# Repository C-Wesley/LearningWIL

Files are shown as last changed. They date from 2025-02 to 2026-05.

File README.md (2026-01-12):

# LearningWIL

**Water Is Life (WIL)** is an Autonomous Surface Vehicle (ASV) developed for Augusta Utilities as part of an internship collaboration with Augusta University.

This repository serves as a learning and continuation guide for future developers. It documents the programming, electronics, and system architecture required to understand and extend WIL.

## Project Overview

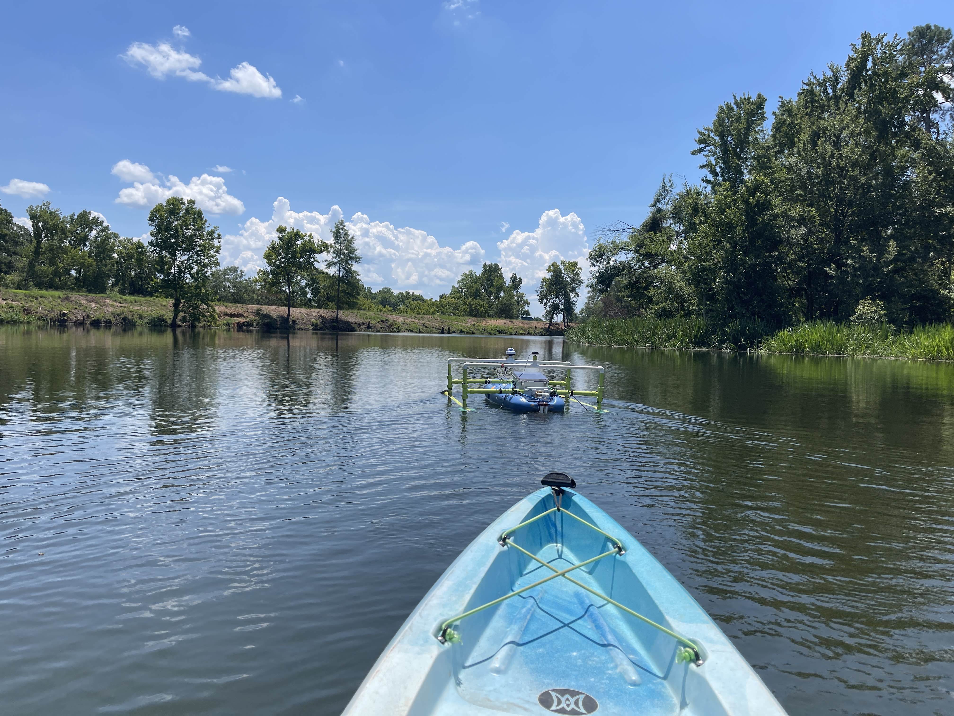
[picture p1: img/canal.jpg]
WIL in the Canal

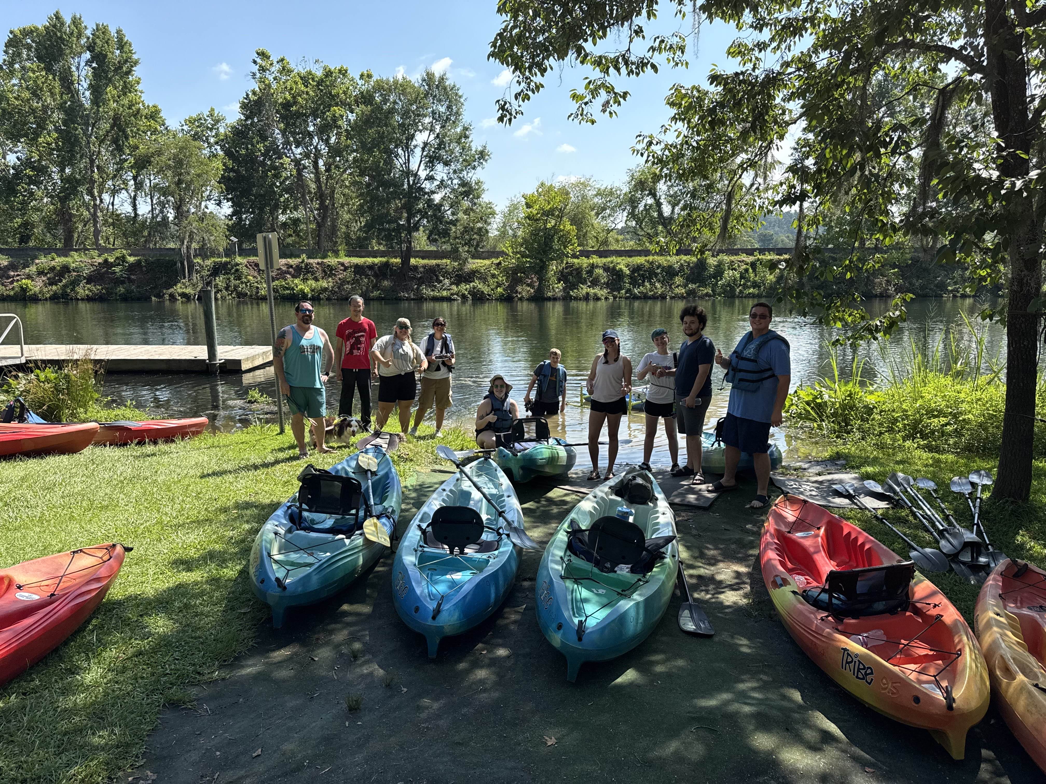
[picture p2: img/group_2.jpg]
WIL canal group RAGU Group Photo

WIL at Lake Olmstead

WIL is designed for environmental data collection and autonomous navigation of local waterways. Development spans embedded programming, sensor integration, data logging, and vehicle controls.

## Repository Structure

### 1. Beginner Examples
`Beginner Examples/`

This is the recommended starting point for new contributors.

- Build circuits 
- Type the code (do not copy–paste)
- Learn how each sensor works in isolation

Suggested exercises:
- Move the IMU and visualize data using the **Arduino Serial Plotter**
- Observe GPS latitude/longitude changes while stationary vs. moving
- Combine GPS, heading, and SD card logging into a simple data logger!

These examples are for you to better understand each sensor individually before trying to throw all of them together. 
They are the 'building blocks' so to speak of WIL. 

### 2. Class-Based Examples
`Class Based Examples/`

These examples introduce **Object-Oriented Programming (OOP)** in C++.

Example:
```cpp
File myFile = ...
```
This creates a `File` object, which:

- Encapsulates data related to files
- Provides methods (functions) that operate on that data

Using classes helps:

- Organize complex systems
- Isolate bugs
- Scale the codebase as features grow

### 3. Notebooks
`Notebooks/`

This directory contains a digital copy of the lab notebooks for WIL. Not every entry is directly related to WIL. Some were more for my own learning. However, there are several useful entries to help you get more familiar with WIL. In the Beginner Examples, I've linked the related entires on each sensors readme file.

### 4. WIL Development Code

`WILDev/`

This directory contains the arudino code running on:

- WIL (Arduino Giga)
- The remote controller (MKR 1310)

Subdirectories:

- `new code/` – current class-based implementation
- `old code/` – old version (no classes)

New development should be based on `new code/`.

## System Architecture

WIL is generally structured around the following diagrams.

 **:TODO:** Update class diagram to reflect latest architecture.

### Class Diagram

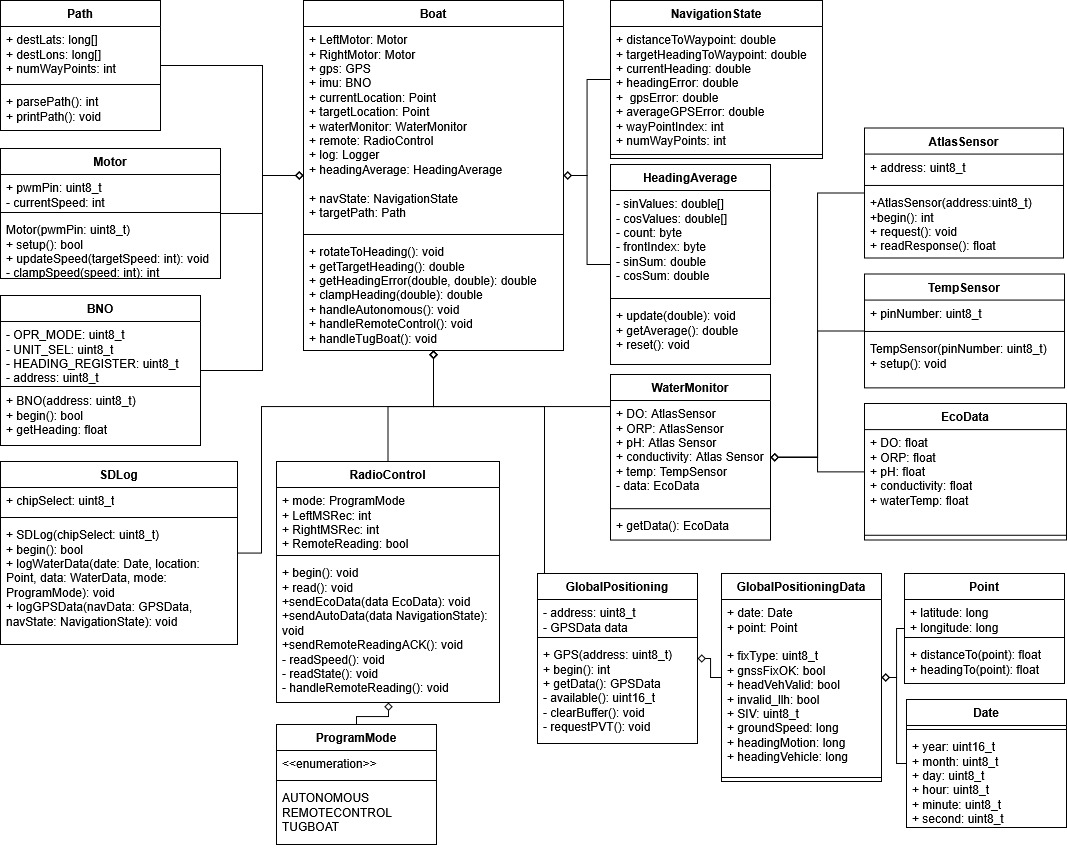
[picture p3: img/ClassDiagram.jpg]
WIL Class Diagram


### Block Diagram

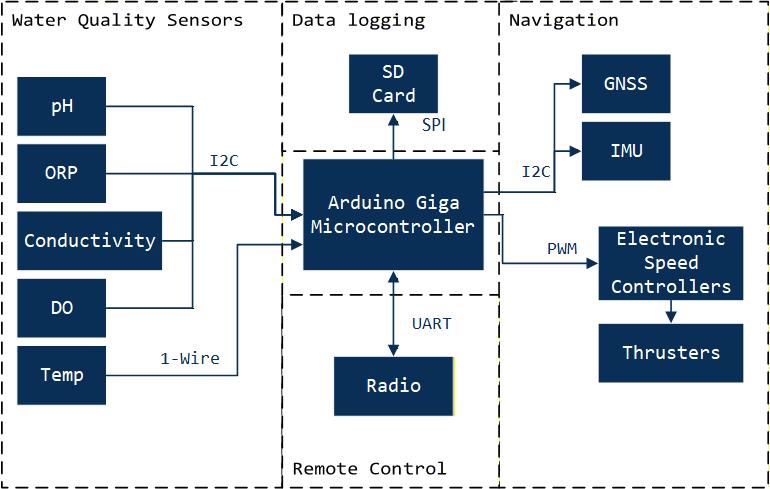
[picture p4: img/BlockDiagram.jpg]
WIL Block Diagram


## Contributing

This repository is designed to be learned from, modified, and extended. Developers are encouraged to:

- Experiment
- Break things
- Document findings
- Improve clarity for the next developer

Water is life (and so is maintainable code).

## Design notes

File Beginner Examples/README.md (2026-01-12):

# Beginner Examples

This folder contains stand-alone Arduino sketches intended to introduce different functionalities of WIL through examples. Each program focuses on one idea at a time to help you learn all the different components of WIL. Here, I am not using classes or object oriented programming because it is easier to learn that way. 
  
These examples are meant to give you understanding of how each subsystem of WIL works as well as build your skills with communication protocols on arduino like I2C, UART, and SPI. 

I recommend building the circuits, typing the code from scratch, and experimenting with each sensor that you use. Typing the code from scratch will help you understand better and aid when reading the entire code base of WIL later on. 

# Recommended Learning Order
- basic_imu
- basic_gps
- basic_sd_card
- basic_thrusters
- basic_sensors
- basic_radio

Most examples have several levels of understanding. Take the GPS for instance. It has both a library version and a non library version. If your goal is to just use the data from the sensor, use the library to make it easy. If your goal is to better understand I2C, take a look at the 'no-library-challenge'. It's not for the faint of heart!

As WIL grew into a more complex system, writing code in the style of these examples became difficult to maintain and extend. To address this, the project transitioned to using classes, which allowed functionality to be separated into well-defined components and enabled data and system state to be encapsulated more cleanly. However, starting here is crucial to your understanding of how the components work and provides a place to experiment, make mistakes, and learn before moving on to more complex programs.

In general, the development approach used throughout this project is to isolate and understand one piece of the system at a time before integrating it into the larger whole. These examples are a direct result of learning how to use individual sensors, peripherals, and interfaces in isolation prior to combining them into a complete system.

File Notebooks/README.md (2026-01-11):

# Lab Notebook entries

## Notebook 1 Contents 
0. [Table of Contents](Notebook_1/0_Table_Of_Contents.pdf)
1. [Arduino MKR 1310 Board](Notebook_1/1_2_Arduino_MKR_1310_Board.pdf)
2. [BNO055 Testing](Notebook_1/3_BNO055_Testing.pdf)
3. [DFRobot GNSS](Notebook_1/4_DFRobot_GNSS.pdf)
4. [Standalone GNSS Data Logger](Notebook_1/5_Standalone_GNSS_Data_Logger.pdf)
5. [Level Shifting MOSFET](Notebook_1/6_Level_Shifting_MOSFET.pdf)
6. [Programming the ALS31313 I2C Address](Notebook_1/7_Programming_the_ALS31313_I2C_address.pdf)
7. [Reyax RYS8839 NEMA Parsing and Logging](Notebook_1/8_Reyax_RYS8839_NEMA_Parsing_and_Logging.pdf)
8. [SparkFun ZED-F9P Logging](Notebook_1/9_Sparkfun_ZED-F9P_Logging.pdf)
9. [Setting Up an RTK Base and Rover System](Notebook_1/10_Setting_up_an_RTK_Base_and_Rover_System.pdf)
10. [BNO055 Relative Heading Observation](Notebook_1/11_BNO055_Relative_Heading_Observation.pdf)
11. [Blue Robotics T200 Underwater Thruster](Notebook_1/12_Blue_Robotics_T200_Underwater_Thruster.pdf)
12. [Autonomous WIL](Notebook_1/13_Autonomous_WIL.pdf)
13. [Writing an H-Bridge Library](Notebook_1/14_Writing_an_H-Bridge_Library.pdf)
14. [Writing an ESC Library](Notebook_1/15_Writing_an_ESC_Library.pdf)
15. [Writing a GPS Library](Notebook_1/16_Writing_a_GPS_Library.pdf)
16. [Writing a BNO Library](Notebook_1/17_Writing_a_BNO_Library.pdf)
17. [Writing a Controller Library](Notebook_1/18_Writing_a_Controller_Library.pdf)
18. [Fixing the Arc](Notebook_1/19_Fixing_the_Arc.pdf)
19. [Writing a Heading Control Library](Notebook_1/20_Writing_a_Heading_control_Library.pdf)
20. [Putting It All Together: Land & Water](Notebook_1/21_22_Putting_it_all_Together_Land_Water.pdf)

## Notebook 2 Contents
0. [Table of Contents](0_Table_of_Contents.pdf)
1. [Land Testing](1_Land_Testing.pdf)
2. [Walking at Lake Olmstead](2_Walking_at_Lake_Olmstead.pdf)
3. [The Better Figure 8](3_The_Better_Figure_8.pdf)
4. [Canal Testing](4_Canal_Testing.pdf)
5. [MB1005 Parksonar Sensor](5_MB1005_Parksonar_Sensor.pdf)
6. [Lidar for Object Detection](6_Lidar_for_Object_Detection.pdf)
7. [Land Testing with Lidar](7_Land_Testing_with_Lidar.pdf)
8. [Revisiting the BNO055](8_Revisiting_the_BNO055.pdf)
9. [Fixing the Negative Heading](9_Fixing_the_Negative_Heading.pdf)
10. [Revisiting the SparkFun GPS](10_Revisiting_the_Sparkfun_GPS.pdf)
11. [Logging and Plotting GPS Data on My Maps](11_Logging_and_Plotting_GPS_Data_on_My_Maps.pdf)
12. [Adding Timestamps from the SparkFun GPS](12_Adding_Timestamps_from_the_Sparkfun_GPS.pdf)
13. [Integrating the New BNO and GPS Code](13_Integrating_the_New_BNO_and_GPS_Code.pdf)
14. [SparkFun GNSS with the Library](14_Sparkfun_GNSS_with_the_library.pdf)
15. [Design Notes](15_Design_Notes.pdf)
16. [Battery Maintenance](16_Battery_Maintenance.pdf)
17. [Basics of SD Card](17_Basics_of_SD_Card.pdf)
18. [Surface Mount Soldering Notes](18_Surface_Mount_Soldering_Notes.pdf)
19. [DOpTC Integration with Arduino Giga](19_DOpTC_Integration_with_Arduino_Giga.pdf)
20. [1-Wire Digital Thermometer DS18B20](20_1-Wire_Digital_Thermometer_DS1B20.pdf)
21. [Introduction to Particle Functions and Variables](21_Introduction_to_Particle_Functions_and_Variables.pdf)
22. [Reading DOpTC Faster](22a_Reading_DOpTC_Faster.pdf)
23. [DOpTC I2C Bus Integration](22_DOpTC_I2C_Bus_Integration.pdf)
24. [Reading the Number of Available Bytes (ZED-F9P)](23_Reading_the_Number_of_Available_Bytes_ZED-F9P.pdf)
25. [Notes on the UBX Protocol for the ZED-F9P](24_Notes_on_the_UBX_Protocol_for_the_ZED-F9P.pdf)
26.  [Reading NAV-PVT on the ZED-F9P without a library](24a_reading_NAVPVT_without_library.pdf)
27. [KiCad Workflow](25_KICAD_Workflow.pdf)
28. [Processing the NAV-PVT Message on ZED-F9P](26_Processing_the_NAV-PVT_Message_on_ZED-F9P.pdf)
29. [Using u-center to Configure the ZED-F9P](27_Uising_U-Center_to_Configure_the_ZED-F9P.pdf)
30. [Loft, Shell, and Boolean Tools in Onshape for Remote Control](28_Loft_Shell_Boolean_tools_Onshape_for_Remote_Control.pdf)
31. [Fitting Data with GNUPlot and Matplotlib](29_Fitting_Data_GNUPlot_and_Matplotlib.pdf)
32. [Eco Test at Lake Olmstead](30_Eco_Test_at_Lake_Olmstead.pdf)
33. [Notes on Floats](31_Notes_on_Floats.pdf)
34. [Serial Radio Basics](32_Serial_Radio_Basics.pdf)
35. [Serial Radio Advanced](32a_Serial_Radio_Advanced.pdf) 
36. [CNC Basics: V-Carve](33_CNC_Basics_V-Carve.pdf)

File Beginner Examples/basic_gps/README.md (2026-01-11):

# Global Navigation Satellite System 
We are using the sparkfun ZED F9P GNSS reciever.  

<a href="https://www.sparkfun.com/sparkfun-gps-rtk-sma-kit.html" target="_blank">Sparkfun GNSS SMA Kit</a>

Objectives:
-Use the Sparkfun GNSS Library to get location information

We used a MKR1310 microcontroller. Any 3.3v logic microcontroller should work. 

<a href="https://docs.arduino.cc/hardware/mkr-wan-1310/" target="_blank">MKR1310</a>

Connections for using I2C:

| MKR1310 |Sparkfun GNSS | 
|--- |---|
| 3.3v | 3.3v | 
| GND | GND |
| SDA | SDA |
| SCL | SCL |

To install the boards manager for the 1310, go to tools -> board -> board manager. 
Search "SAMD" and look for the arduino SAMD boards.

To install the library go to tools -> manage libraries
Search "SparkFun GNSS v3".

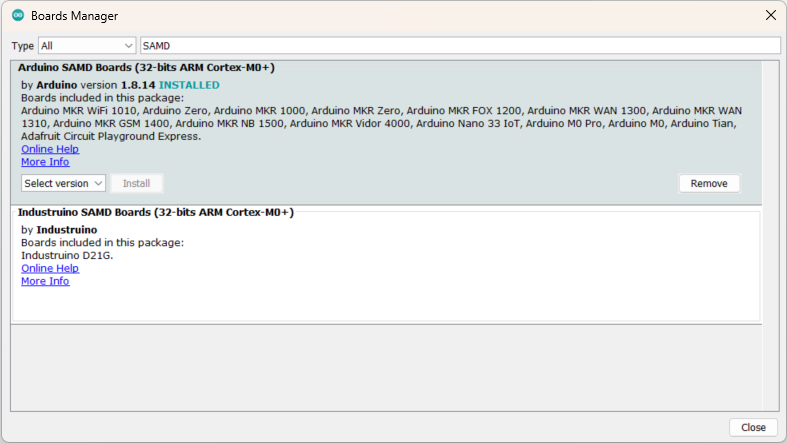
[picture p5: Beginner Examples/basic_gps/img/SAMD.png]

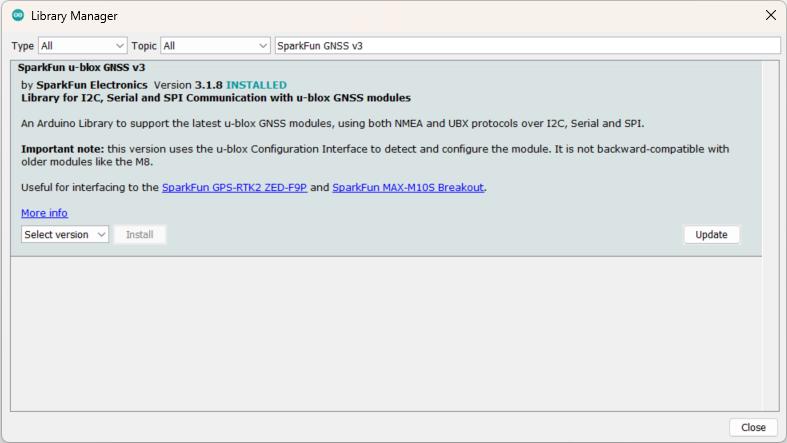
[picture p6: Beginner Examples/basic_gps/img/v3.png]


## u-blox ZED-F9P GNSS (I²C)

**What the Program Does**
- Initializes a ZED-F9P GNSS module
- Reads:
  - Latitude and longitude
  - Time and date
  - Satellites in view (SIV)
- Prints raw GNSS data to Serial

# Related Lab Notebook Entries

## No-Library-Challenege 
[Revisiting the ZED-F9P](https://c-wesley.github.io/projects/asv/Notebook_2/10_Revisiting_the_Sparkfun_GPS.pdf)

[Reading the Number of Available Bytes ZED-F9P](https://c-wesley.github.io/projects/asv/Notebook_2/23_Reading_the_Number_of_Available_Bytes_ZED-F9P.pdf)

[Notes on the UBX Protocol for the ZED-F9P](https://c-wesley.github.io/projects/asv/Notebook_2/24_Notes_on_the_UBX_Protocol_for_the_ZED-F9P.pdf)

[Reading the NAV-PVT on the ZED-F9P without a Library](https://c-wesley.github.io/projects/asv/Notebook_2/24a_reading_NAVPVT_without_library.pdf)

[Processing the NAV-PVT Message on the ZED-F9P](https://c-wesley.github.io/projects/asv/Notebook_2/26_Processing_the_NAV-PVT_Message_on_ZED-F9P.pdf)

[Using U-Center to Configure the ZED-F9P](https://c-wesley.github.io/projects/asv/Notebook_2/27_Uising_U-Center_to_Configure_the_ZED-F9P.pdf)

## SparkFun GNSS V3 Library 

[SparkFun ZED-F9P Data Logger](https://c-wesley.github.io/projects/asv/Notebook_1/9_Sparkfun_ZED-F9P_Logging.pdf)

[SparkFun GNSS with the Library](https://c-wesley.github.io/projects/asv/Notebook_2/14_Sparkfun_GNSS_with_the_library.pdf)

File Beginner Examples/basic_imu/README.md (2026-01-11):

# BNO055 IMU

This sketch does the following: 

- Scans the I²C bus to confirm the BNO055 address (0x28)
- Configures the BNO055:
- - uses the accelerometer and gyroscope in a fusion mode
- - Sets output units to degrees
- Reads the heading registers (0x1A and 0x1B)
- Combines the raw bytes and converts them to degrees

# Related Lab Notebook Entries

## No-Library-Challenge
[Revisiting the BNO055](https://c-wesley.github.io/projects/asv/Notebook_2/8_Revisiting_the_BNO055.pdf)

## Adafruit_Sensor and Adafruit_BNO055 Library
[BNO055 Testing](https://c-wesley.github.io/projects/asv/Notebook_1/3_BNO055_Testing.pdf)

The following resource was used when making the above: 
[Paul McWhorter IMU Videos](https://toptechboy.com/arduino-based-9-axis-inertial-measurement-unit-imu-based-on-bno055-sensor/)

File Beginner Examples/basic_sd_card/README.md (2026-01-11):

# SD Card
These files show the basics of using the sd card. 
The main objectives here are to:
- Initalize SD Card
- Handle SD errors
- Write to a file
- Determine if a file already exists
- Delete a file if it exists
- Extract data from a file into appropriate data types

## SD Card Write & Read

### Example 1: Writing and Reading a File

**What the Program Does**
- Initializes an SD card
- Deletes an existing file if present
- Writes text and numeric data to `data.txt`
- Reopens the file and prints its contents to Serial
---

### Example 2: Reading and Parsing a CSV File

**What the Program Does**
- Opens a CSV file (`path.csv`)
- Reads one line at a time
- Parses ID, longitude, and latitude fields
- Prints parsed data to Serial

Begin by looking at SD_Card_RW. 
Then move onto path_parse.

An advanced user may find the SD class and File class API useful (Located near the bottom of the page): 

<a href="https://docs.arduino.cc/libraries/sd/#SD%20class" target="_blank">Arduino SD Class API</a>

<a href="https://docs.arduino.cc/libraries/sd/#File%20class" target="_blank">Arduino File Class API</a>

The following connections need to be made to an appropriate microcontroller: 
For the purpose of this demonstration, we are using a 3.3v microsd card reader, so we opted for the arduino mkr1310 board for it's 3.3v logic. Chip select may be any unused digital pin. 

|SD Card| MKR1310 |
|---|---|
|MOSI | MOSI |
|MISO | MISO |
|SCK | SCK |
|CS | 5 |
|PWR | VCC | 
|GND | GND | 

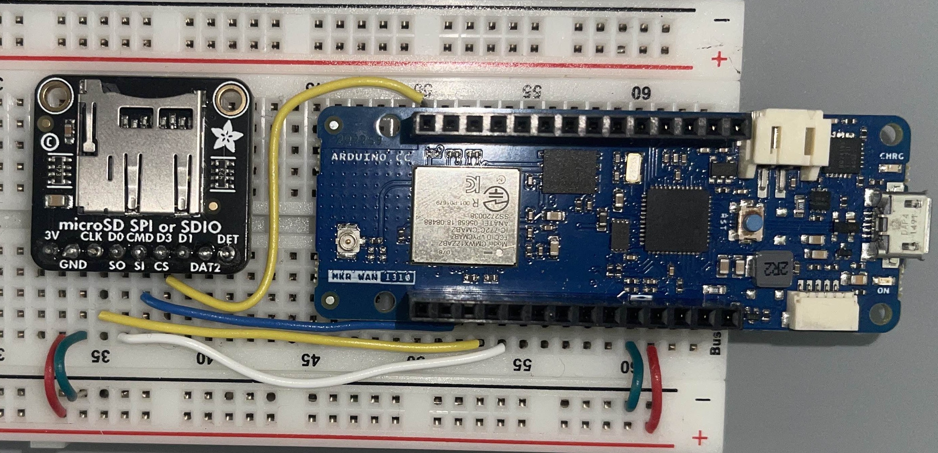
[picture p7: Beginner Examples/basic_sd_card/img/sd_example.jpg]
Example Connections

Figure 1. Example connections to the MKR 1310 board. 

# Related Lab Notebook Entries

[Basics of SD Card](https://c-wesley.github.io/projects/asv/Notebook_2/17_Basics_of_SD_Card.pdf)

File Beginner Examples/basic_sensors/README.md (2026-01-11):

# Related Lab Notebook Entires

[Reading DOpTC Faster](https://c-wesley.github.io/projects/asv/Notebook_2/22a_Reading_DOpTC_Faster.pdf)

[1-Wire Digitasl Thermometer DS18B20 (No Library)](https://c-wesley.github.io/projects/asv/Notebook_2/20_1-Wire_Digital_Thermometer_DS1B20.pdf)

## Older Implementation but still may be of use
[DOpTC Integration with Arduino Giga](https://c-wesley.github.io/projects/asv/Notebook_2/19_DOpTC_Integration_with_Arduino_Giga.pdf)

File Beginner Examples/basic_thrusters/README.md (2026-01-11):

# Thruster Controls
We are using two Blue Robotics T200 thrusters and their Basic Electronic Speed Controllers (ESC).

<a href="https://bluerobotics.com/store/thrusters/t100-t200-thrusters/t200-thruster-r2-rp/" target="_blank">T200 Thruster</a>

<a href="https://bluerobotics.com/store/thrusters/speed-controllers/besc30-r3//" target="_blank">Basic ESC</a>

<a href="https://bluerobotics.com/store/comm-control-power/powersupplies-batteries/battery-lp-4s-10ah/" target="_blank"> Lithum Polymer Battery </a>

Objectives:
-Understand PWM Control of T200's
-Use the Serial Monitor to test different speeds

The T200 thrusters use a three phase brushless motor.
You can think of each phase as a separate coil that is wraped around a stator. 
These coils are energized following a pattern to make the rotor spin. See diagram below. 

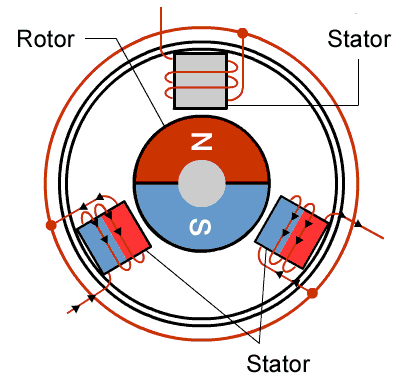
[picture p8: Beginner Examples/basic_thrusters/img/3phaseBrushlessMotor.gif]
Three Phase Motor Diagram


Example Wiring Diagram: 
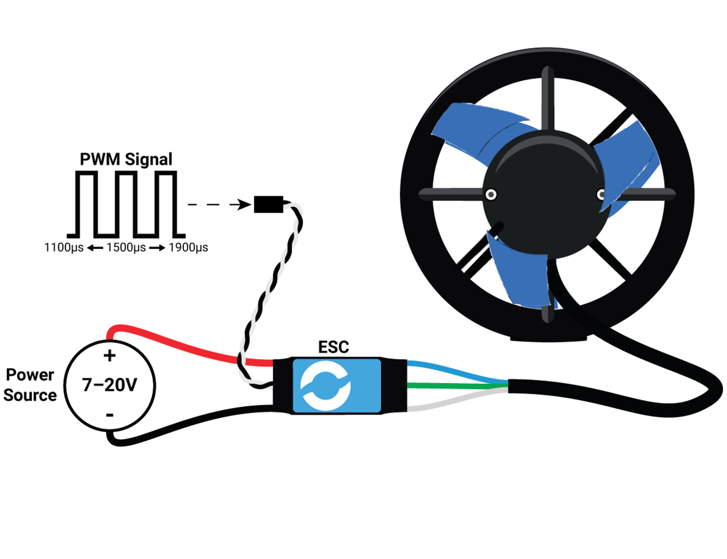
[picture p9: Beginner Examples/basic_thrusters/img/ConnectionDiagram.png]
Example Wiring Diagram


We don't directly control the three phase connections. Instead we use an ESC. The ESC requires a PWM signal from the microcontroller and power from a battery. We have a wiring harness that allows us to power two ESC's in parallel. 

PWM stands for Pulse Width Modulation. Typically, we don't varry the period of this signal, but instead only vary the duty cycle. However the T200 thrusters required a very specific PWM signal. 

It's wants a signal with a 20ms period and a high pulse of between 1100 -1900 microseconds, centered at 1500. That means when we set our PWM to have a high signal for 1500 microseconds, the motors will be turnd off. 

|High Pulse Time(us)|Motor Direction | 
|--- |---|
| 1475-1525 | OFF | 
| 1100-1475 | REVERSE |
| 1525-1900 | FORWARD |

This is the same idea with servo motors: The 90 degrees would coresspond to our thrusters being off. The 0 degrees is full throttle reverse and the 180 degrees is full throttle forwards. In this manner, you can either hook up servos to check that the motor control is working properly, or you can hook up to a scope to see the PWM singal being generated. 
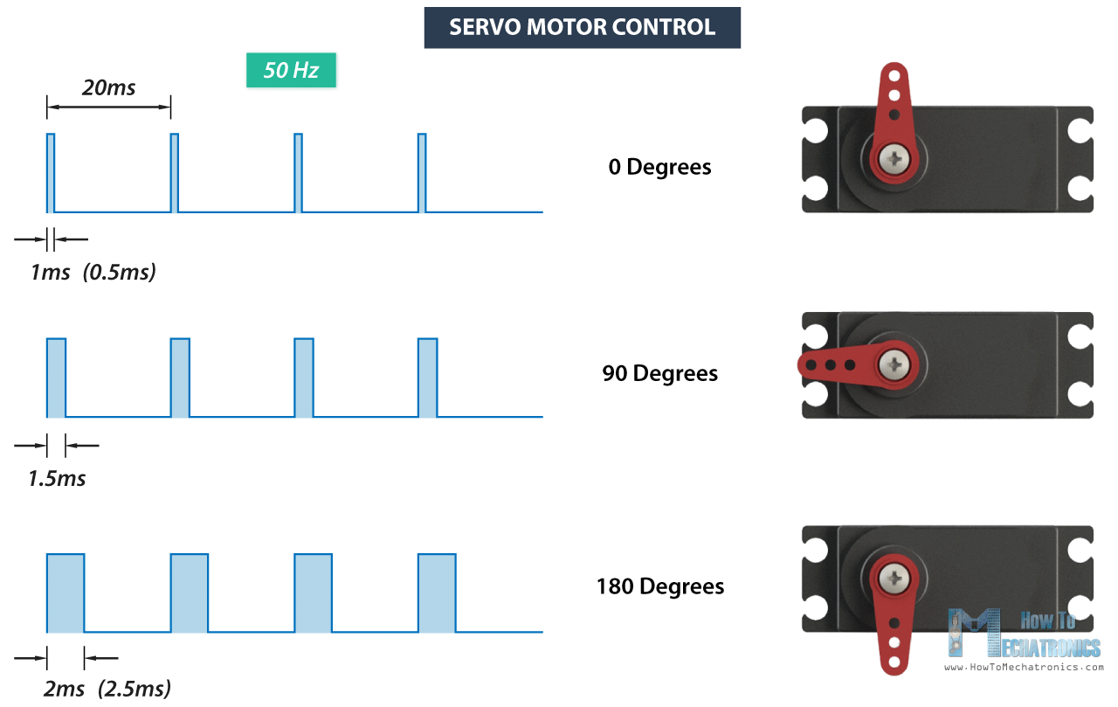
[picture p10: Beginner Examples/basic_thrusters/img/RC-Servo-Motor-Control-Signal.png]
Servo Motor Control


# Related Lab Notebook Entires

[Blue Robotics T200 Underwater Thruster](https://c-wesley.github.io/projects/asv/Notebook_1/12_Blue_Robotics_T200_Underwater_Thruster.pdf)

[Battery Maintenance](https://c-wesley.github.io/projects/asv/Notebook_2/16_Battery_Maintenance.pdf)

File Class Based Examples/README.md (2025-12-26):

# Class Based Examples

## Overview
- These examples are derived from subsystems used in the WIL (Water Is Life) autonomous surface vehicle. Reviewing them before modifying the main WIL codebase will make it easier to understand how the individual components fit together.
- The examples assume some familiarity with C++ classes. If object-oriented programming is new to you, it may be helpful to review introductory material on C++ classes before working through these files.
- Examples are grouped by intended functionality; some headers like `types.h` appear in multiple folders, and some examples build on concepts introduced in earlier ones.

### C++ Class & OOP Tutorials
- Object-oriented programming is a broad topic, and it is common to spend years gradually becoming more comfortable with it. For the purposes of this project, however, only a small and practical subset of OOP concepts is required. The goal here is not mastery, but building enough understanding to read, use, and modify the WIL code with confidence.

- https://paulmurraycbr.github.io/ArduinoTheOOWay.html

- https://www.geeksforgeeks.org/cpp/object-oriented-programming-in-cpp/

- https://www.geeksforgeeks.org/cpp/c-classes-and-objects/

- https://www.learncpp.com/cpp-tutorial/introduction-to-object-oriented-programming/

## Design Philosophy

The examples in this repository follow a few guiding principles:

- **Separation of concerns**  
  Data definitions (`types.h`) are kept separate from logic and hardware interaction.

- **Self-contained modules**  
  Each test folder can be compiled and understood independently.

- **Clarity over cleverness**  
  Code prioritizes readability and learning value over extreme optimization.

## Recommended Learning Order
1. test_imu
2. test_gps
3. test_sensors
4. test_motor
5. test_sd
6. test_radio

## Typical layout 
| Path | Description |
| ---  | --- |
| /test_functionality | Contains code for \[functionality\] |
|  &emsp;- types.h | local copy of shared types |
|  &emsp;- config.h | local copy of configuration variables |
|  &emsp;- functionality.h | Header file that contains the class definition |
|  &emsp;- test_functionality.ino | Example of using the class |

## What are structures and classes? 
A structure is a collection of like or related variables under some name. Structures don't have methods defined inside of them, but a function can be written that takes in a structure. 

A class is a collection of variables and their associated methods together. In pure C programming, you only have structures. But in C++, you have access to classes. 

## Purpose of `types.h`
- Defines common types, typedefs, and shared structs and classes used across examples.
- Serves to keep examples self-contained so each module can compiled independently.
- Classes like `Point` and `HeadingAverage` encapsulate math that would otherwise be duplicated.
- Avoid modifying `types.h` inside individual test folders unless explicitly experimenting. 
- Do not mix degrees and radians — all public interfaces use degrees.

## Explanation of Types

### `class Point`

The `Point` class represents a geographic location defined by latitude and longitude.

It also encapsulates navigation-related computations, such as:
- Distance between two points
- Required heading to reach another point

#### Members

| Member | Type | Description |
|---|---|---|
| `latitude` | `long` | Latitude in degrees × 10⁻⁶ |
| `longitude` | `long` | Longitude in degrees × 10⁻⁶ |

> Using a long data type avoids floating-point errors and is commonly used in GPS systems.

#### Constructors

- **Default constructor**  
  Initializes the point at `(0, 0)`.

- **Parameterized constructor**  
  Accepts latitude and longitude directly.

#### Methods

##### `double distanceTo(const Point& other) const`

Computes the great-circle distance (in meters) between this point and another point using spherical Earth geometry.

- Uses Earth radius: 6,372,795 meters
- Does not modify either point

##### `double getTargetHeading(const Point& other) const`

Computes the heading (bearing) required to travel from this point to another.

- Output range: \[0, 360\) degrees
- North = 0°, East = 90°, South = 180°, West = 270°
---
### `struct Date`

Represents a timestamp, typically sourced from the GPS module.

#### Members

| Member | Type | Description |
|---|---|---|
| `year` | `uint16_t` | Year |
| `month` | `uint8_t` | Month |
| `day` | `uint8_t` | Day |
| `hour` | `uint8_t` | Hour |
| `minute` | `uint8_t` | Minute |
| `second` | `uint8_t` | Second |
---
### `struct GlobalPositioningData`

Aggregates all GPS-related data into a single structure.

This struct is typically populated directly from the GNSS module and used by navigation and control logic.

#### Members

| Member | Type | Description |
|---|---|---|
| `date` | `Date` | GPS-provided timestamp |
| `position` | `Point` | Current latitude and longitude |
| `fixType` | `uint8_t` | GNSS fix type |
| `gnssFixOK` | `bool` | Valid GNSS fix flag |
| `headVehValid` | `bool` | Vehicle heading validity |
| `invalid_llh` | `bool` | Invalid lat/long/height flag |
| `SIV` | `uint8_t` | Satellites in view |
| `groundSpeed` | `long` | Ground speed (mm/s) |
| `headingMotion` | `long` | Motion heading (degrees × 10⁻⁵) |
| `headingVehicle` | `long` | Vehicle heading (degrees × 10⁻⁵) |
---
### `struct NavigationState`

Represents the current navigation and control state of WIL.

#### Members

| Member | Type | Description |
|---|---|---|
| `distanceToWaypoint` | `double` | Distance to target waypoint (meters) |
| `targetHeading` | `double` | Desired heading \[0–360°\) |
| `currentHeading` | `double` | Measured heading \[0–360°\) |
| `headingError` | `double` | Normalized heading error `[-1, 1]` |
| `gpsError` | `double` | Difference between GPS and heading sensor |
| `averageGPSError` | `double` | Running average of GPS error |
| `waypointIndex` | `int` | Current waypoint index |
| `numWaypoints` | `int` | Total number of waypoints |
---
### `struct EcoData`

Stores measurements from environmental sensors.

#### Members

| Member | Type | Description |
|---|---|---|
| `DO` | `float` | Dissolved Oxygen |
| `ORP` | `float` | Oxidation-Reduction Potential |
| `pH` | `float` | pH level |
| `conductivity` | `float` | Electrical conductivity |
| `waterTemp` | `float` | Water temperature (°C) |
---
### `enum ProgramMode`

Defines the operating mode of WIL.

#### Values

| Mode | Value | Description |
|----|---|---|
| `REMOTECONTROL` | `0` | Manual operator control |
| `AUTONOMOUS` | `1` | Fully autonomous navigation |
| `TUGBOAT` | `2` | Assisted or towing behavior |
---
### `class HeadingAverage`

Implements a circular buffer and vector averaging for averaging heading angles.

Because angles wrap around (e.g., 359° → 0°), a simple arithmetic mean does not work.  
This class instead averages sine and cosine components, producing a correct circular mean.

#### Methods

- `update(double angleDegrees)` — Adds a new heading sample
- `get()` — Returns the averaged heading (degrees)
- `reset()` — Clears internal state

## Build & usage
- Each module can be built independently. Connect the appropriate hardware.

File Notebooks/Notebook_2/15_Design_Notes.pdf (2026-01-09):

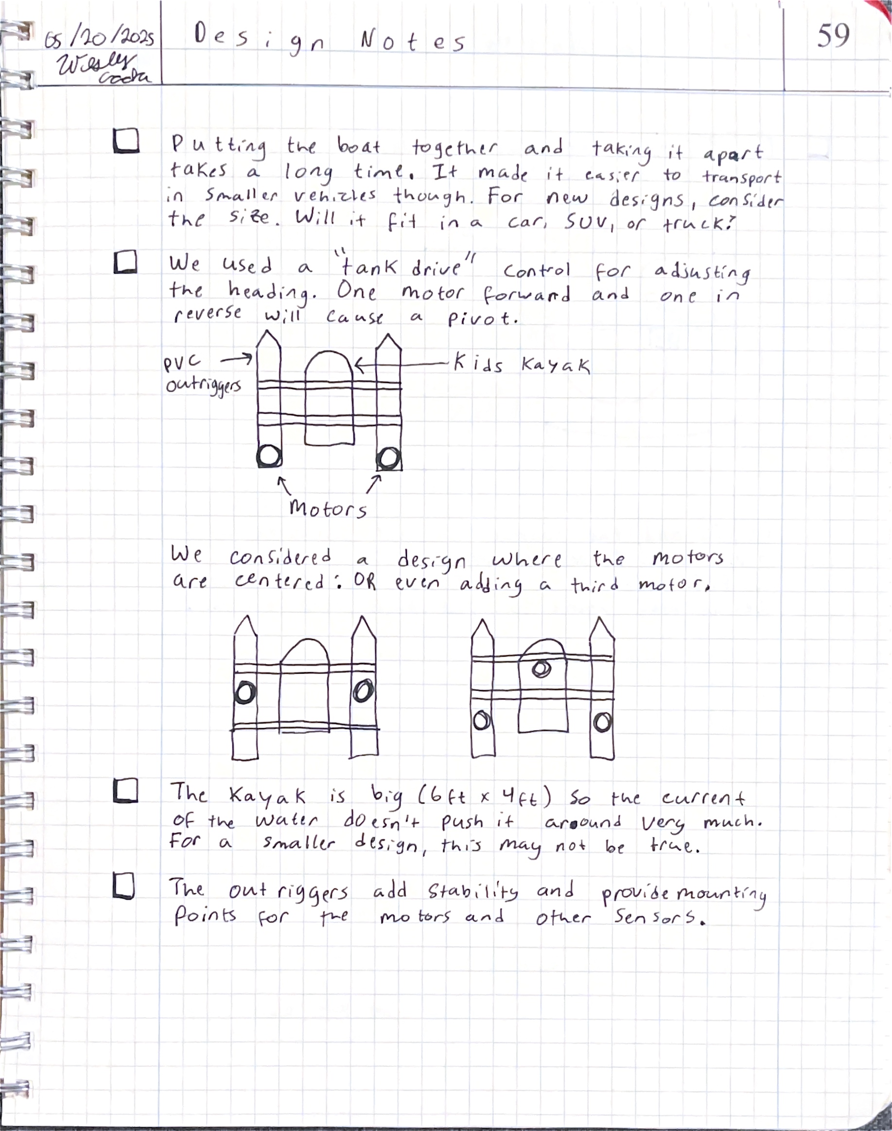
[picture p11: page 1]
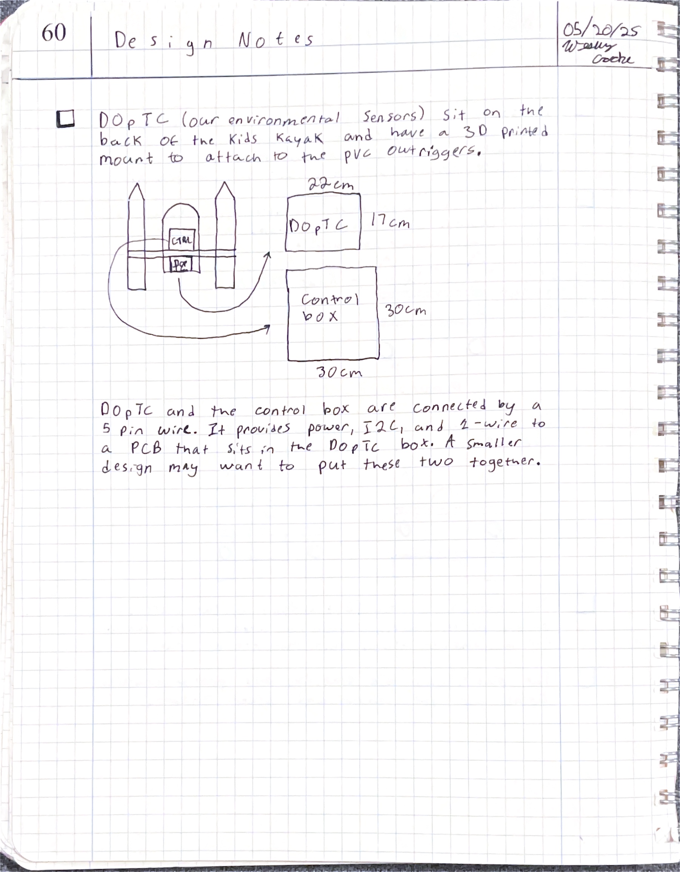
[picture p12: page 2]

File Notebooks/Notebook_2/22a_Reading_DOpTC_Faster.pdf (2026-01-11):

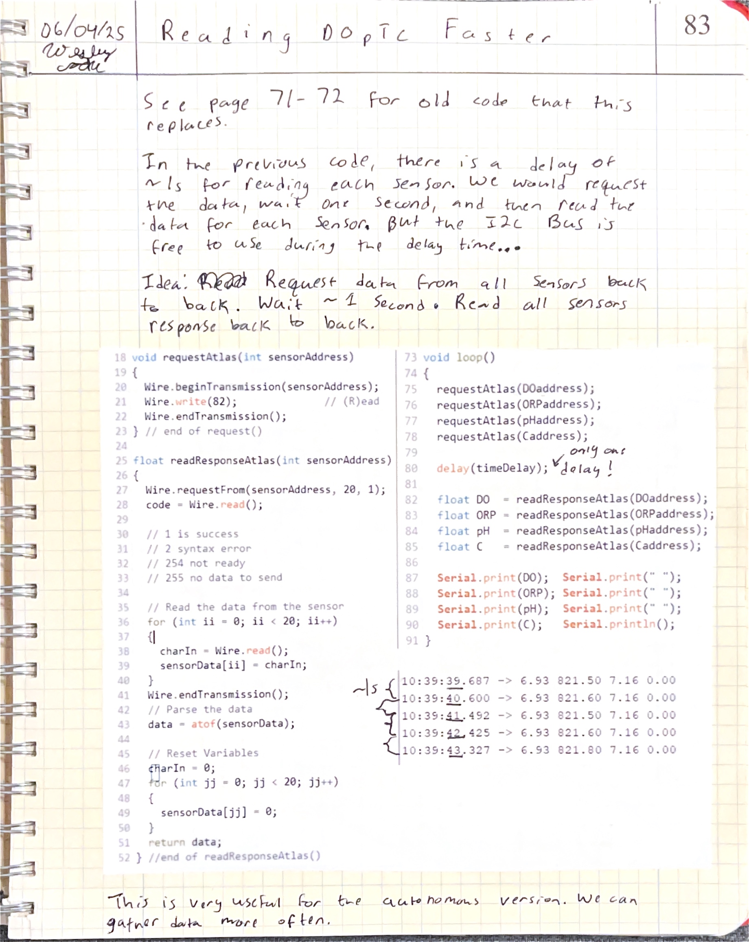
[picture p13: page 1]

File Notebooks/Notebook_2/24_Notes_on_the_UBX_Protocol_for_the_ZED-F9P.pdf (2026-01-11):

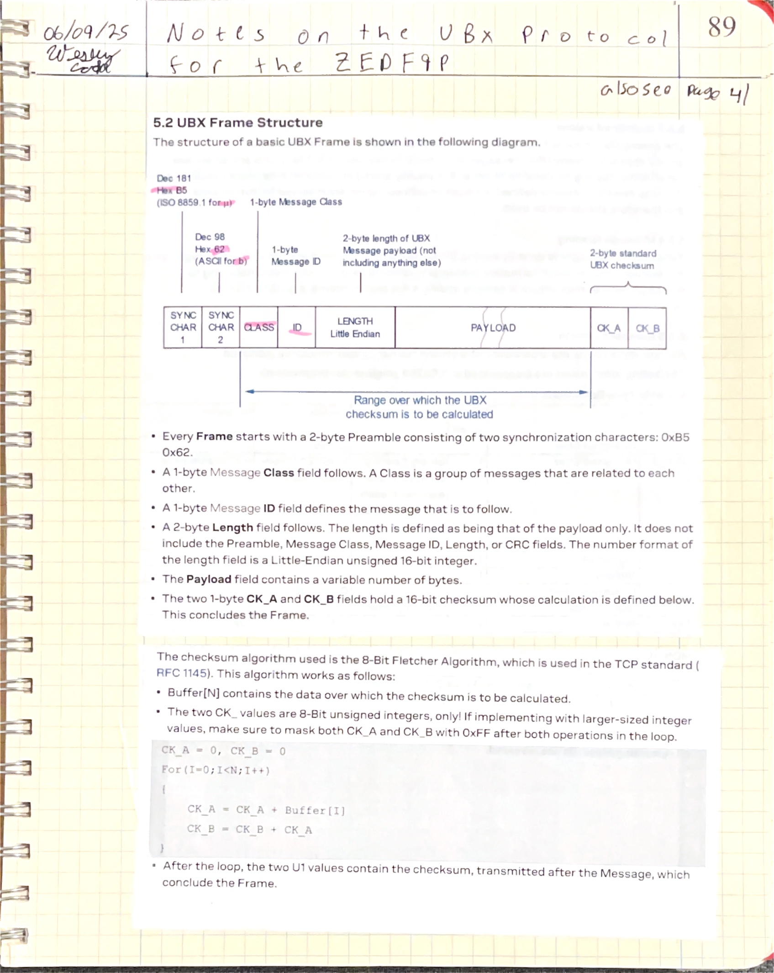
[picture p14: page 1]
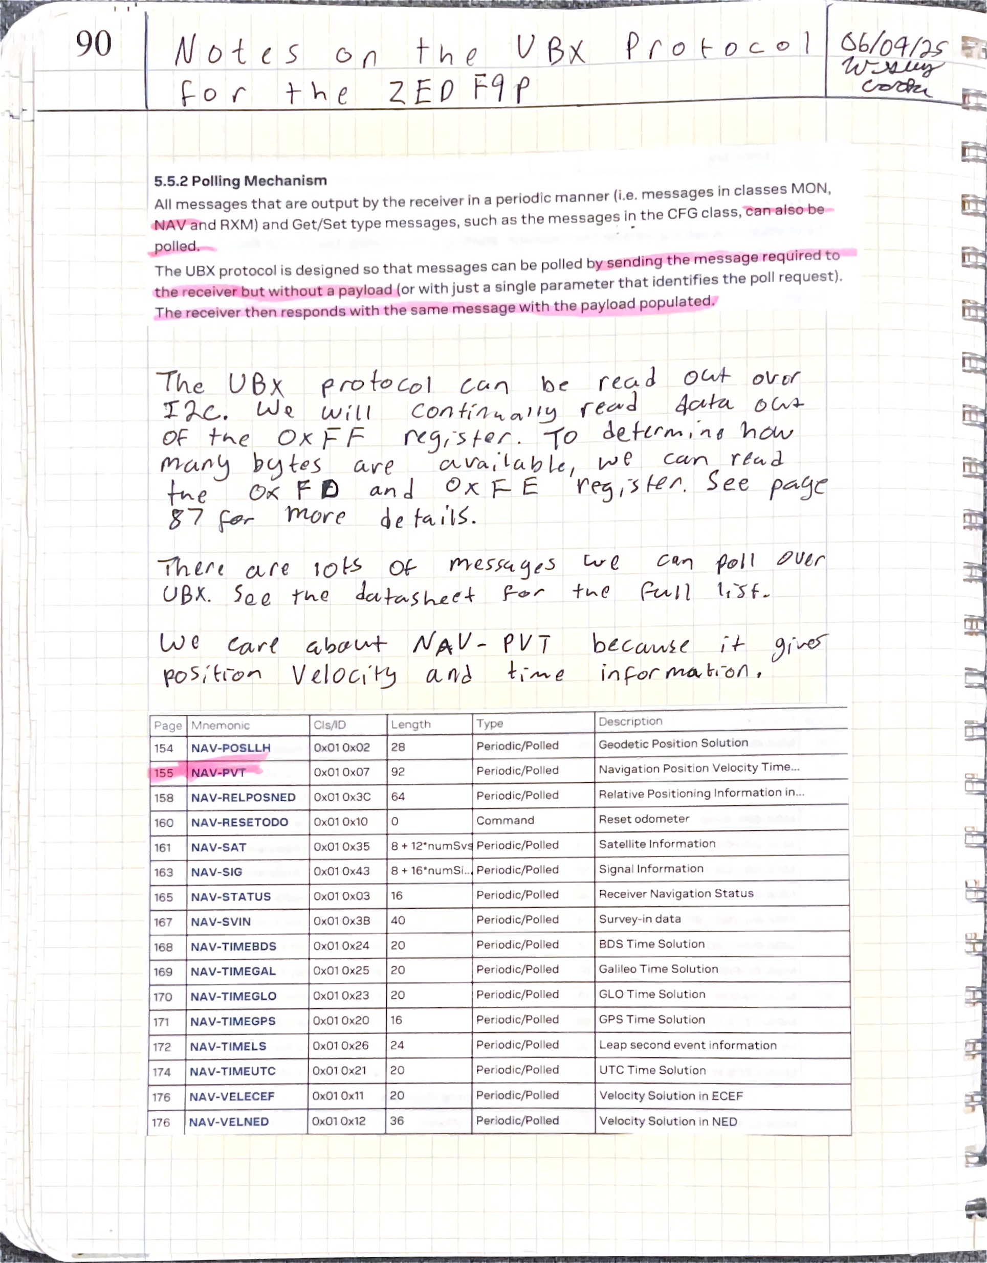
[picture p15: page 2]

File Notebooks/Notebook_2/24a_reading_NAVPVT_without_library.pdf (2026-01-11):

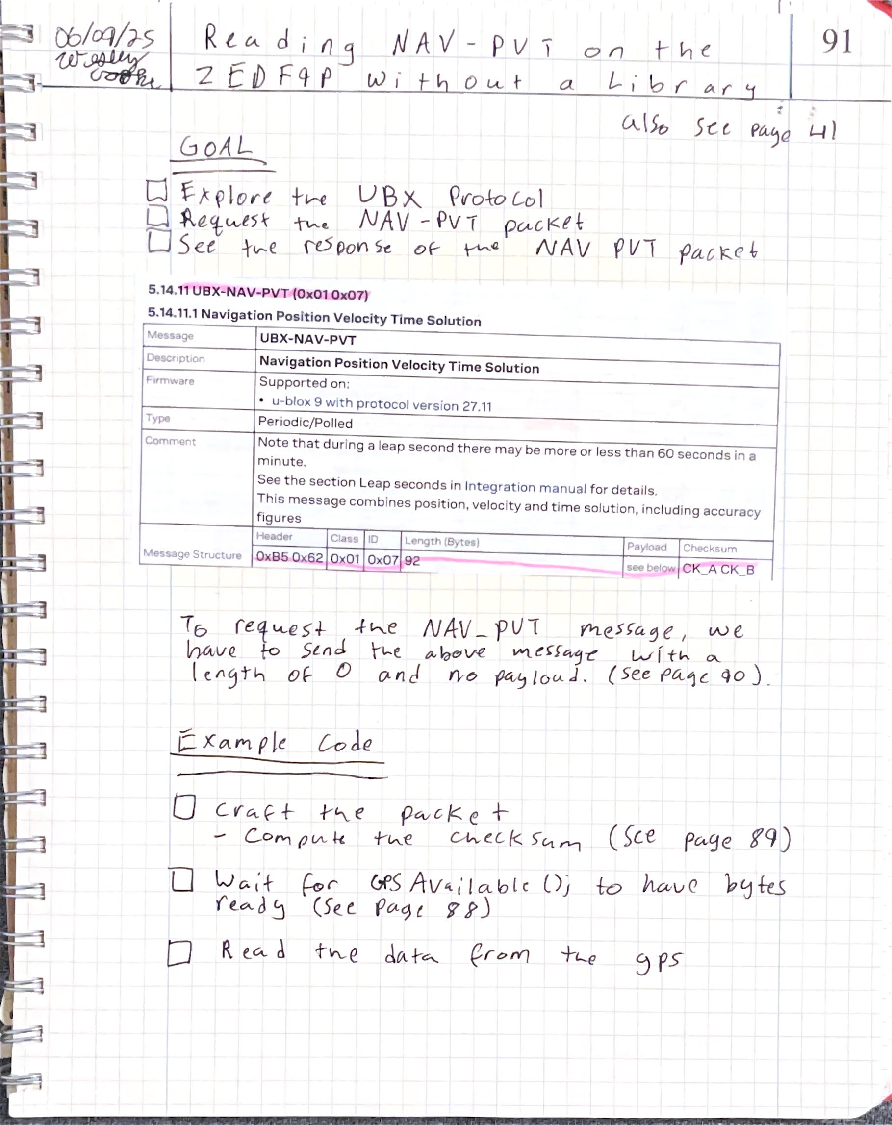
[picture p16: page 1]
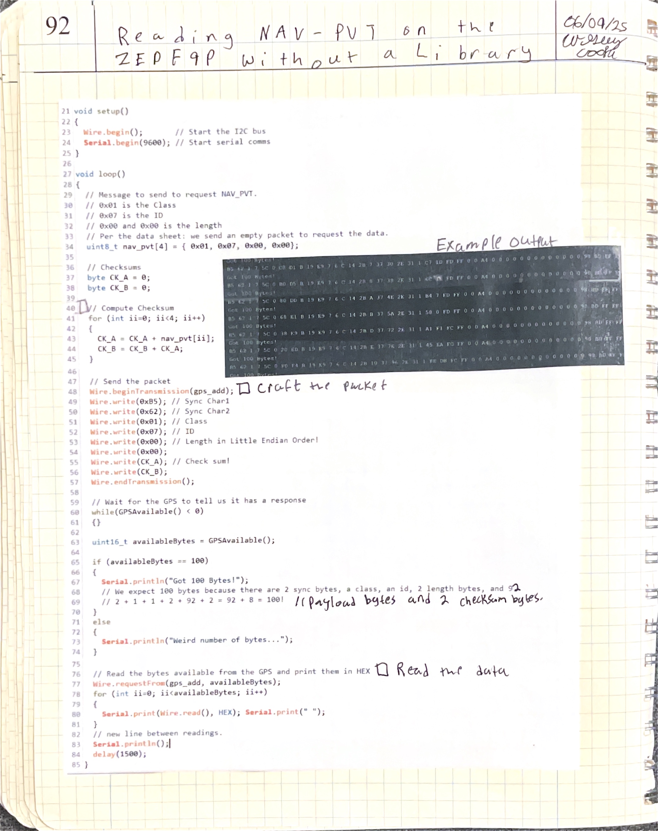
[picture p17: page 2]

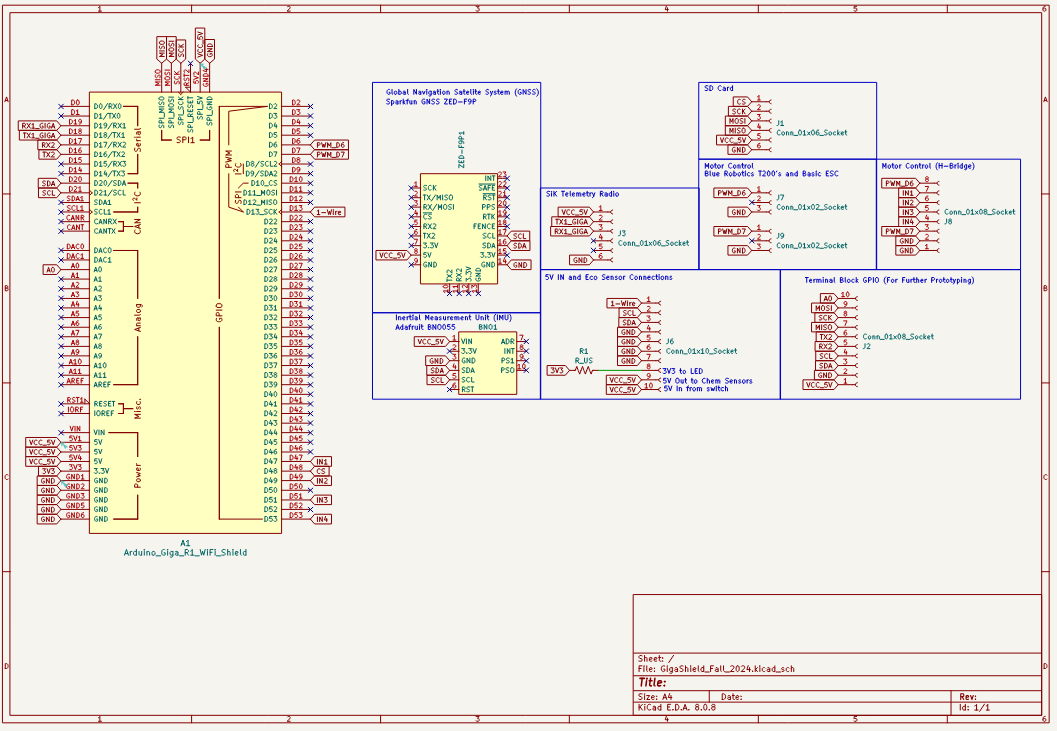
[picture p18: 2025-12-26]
WILDev/PCB/img/Schematic.png

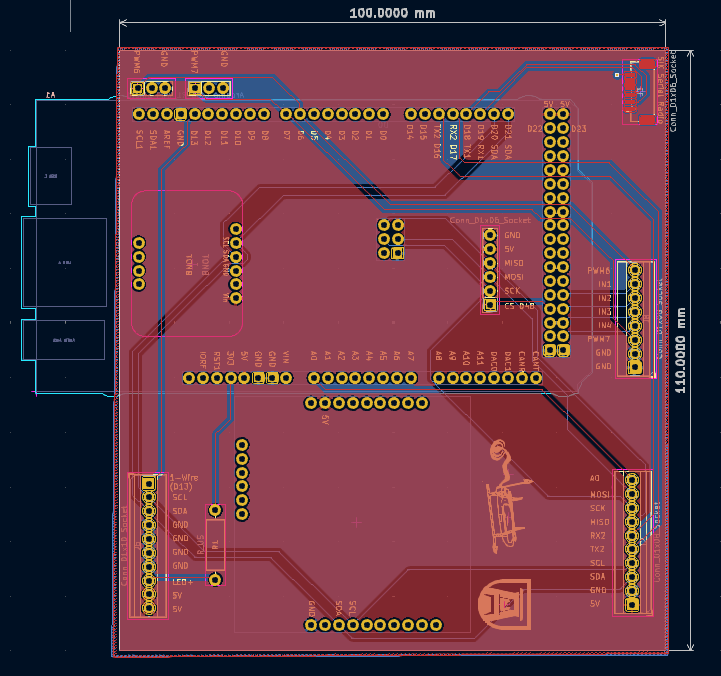
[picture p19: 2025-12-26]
WILDev/PCB/img/Layout.png

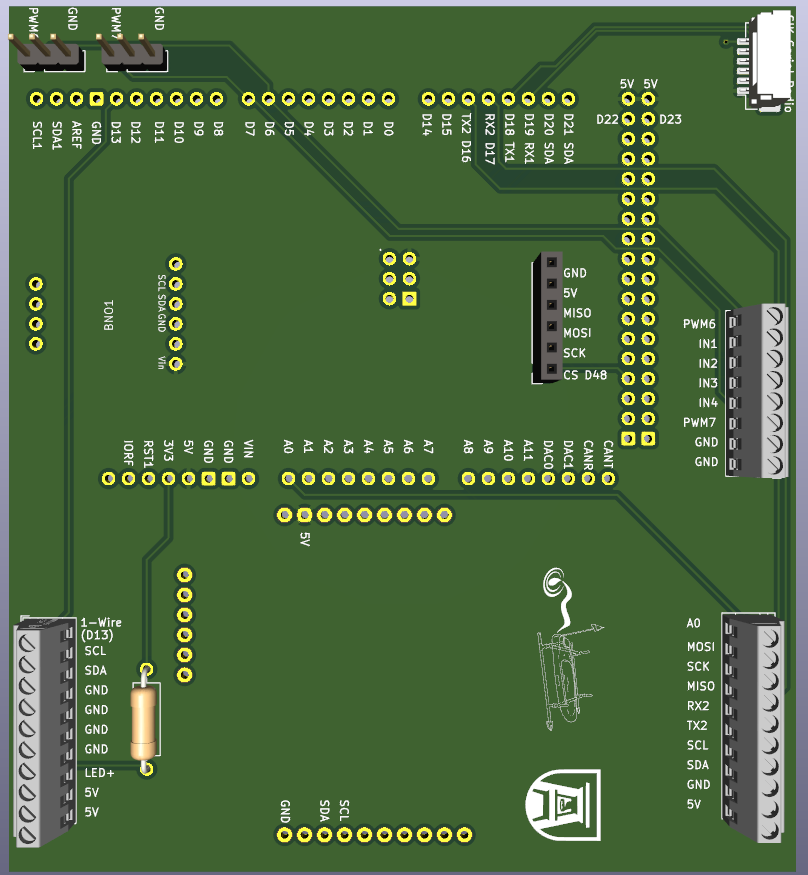
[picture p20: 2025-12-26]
WILDev/PCB/img/3dModel.png

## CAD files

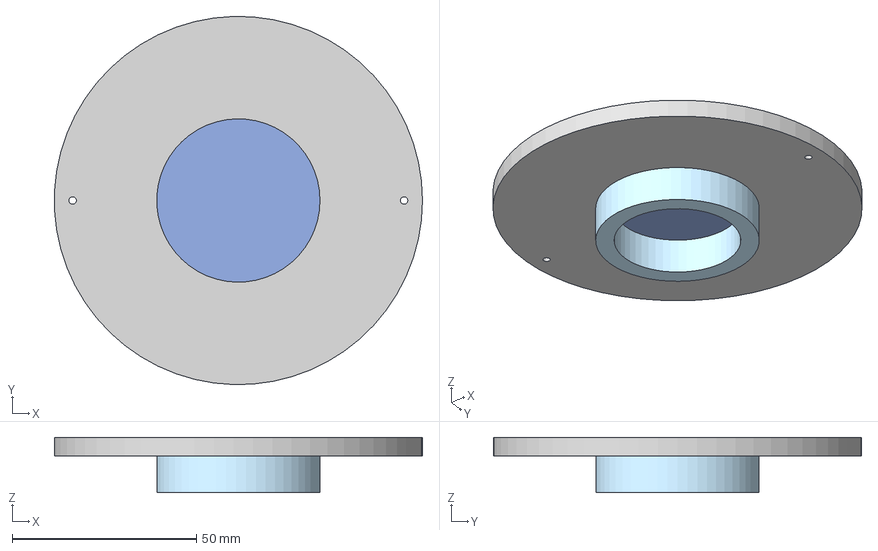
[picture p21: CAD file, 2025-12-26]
WILDev/CAD/Compass Mount/CompassMount.step
99.9 x 100.0 x 15.0 mm

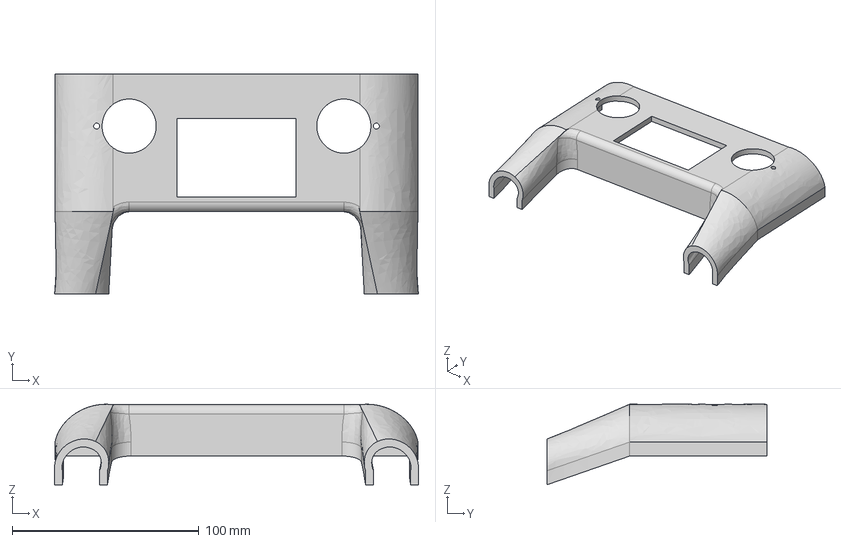
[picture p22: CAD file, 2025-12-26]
WILDev/CAD/Controller/STEP/ControllerTop.step
195.0 x 117.9 x 43.2 mm

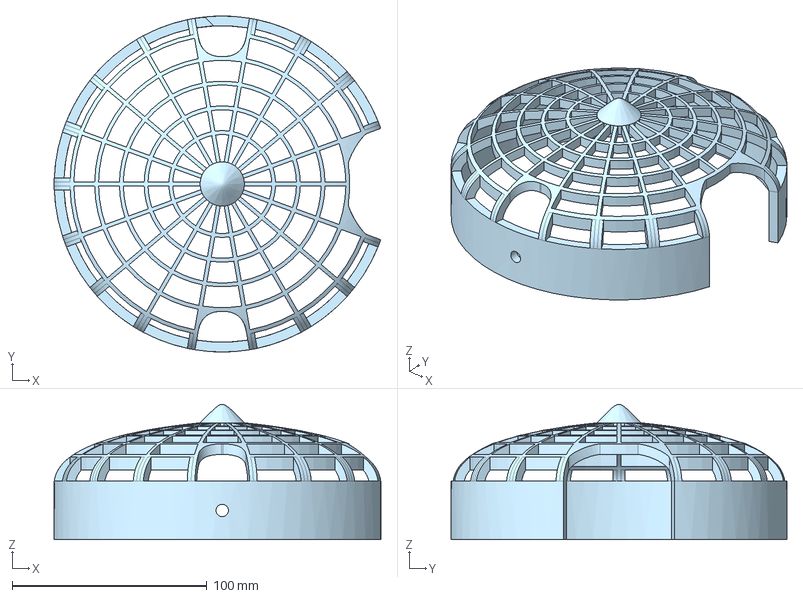
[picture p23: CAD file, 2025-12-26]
WILDev/CAD/Motor Guard/Motor Mount.step
167.7 x 172.6 x 69.5 mm

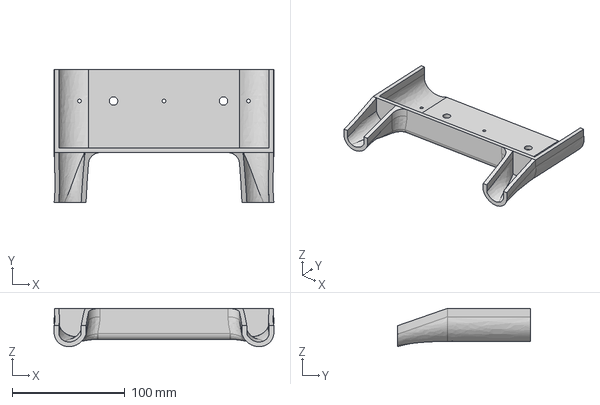
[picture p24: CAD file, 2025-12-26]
WILDev/CAD/Controller/STEP/ControllerBottom.step
195.1 x 117.9 x 33.9 mm

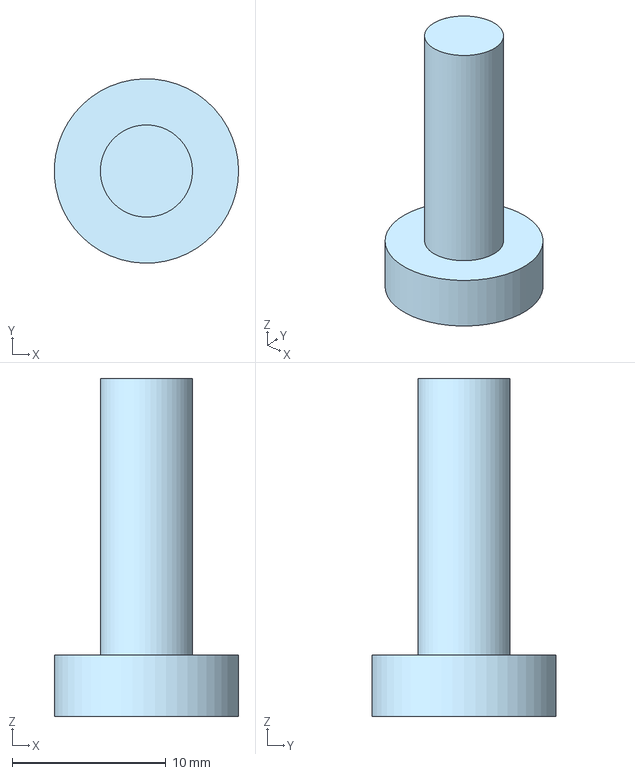
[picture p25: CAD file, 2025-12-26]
WILDev/CAD/Controller/STEP/ButtonExtension.step
12.0 x 12.0 x 22.0 mm

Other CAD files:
WILDev/CAD/Compass Mount/CompassMount.x_t
WILDev/CAD/Controller/PARASOLID/ButtonExtension.x_t
WILDev/CAD/Controller/PARASOLID/ControllerBottom.x_t
WILDev/CAD/Controller/PARASOLID/ControllerTop.x_t
WILDev/CAD/Motor Guard/Motor Guard.x_t

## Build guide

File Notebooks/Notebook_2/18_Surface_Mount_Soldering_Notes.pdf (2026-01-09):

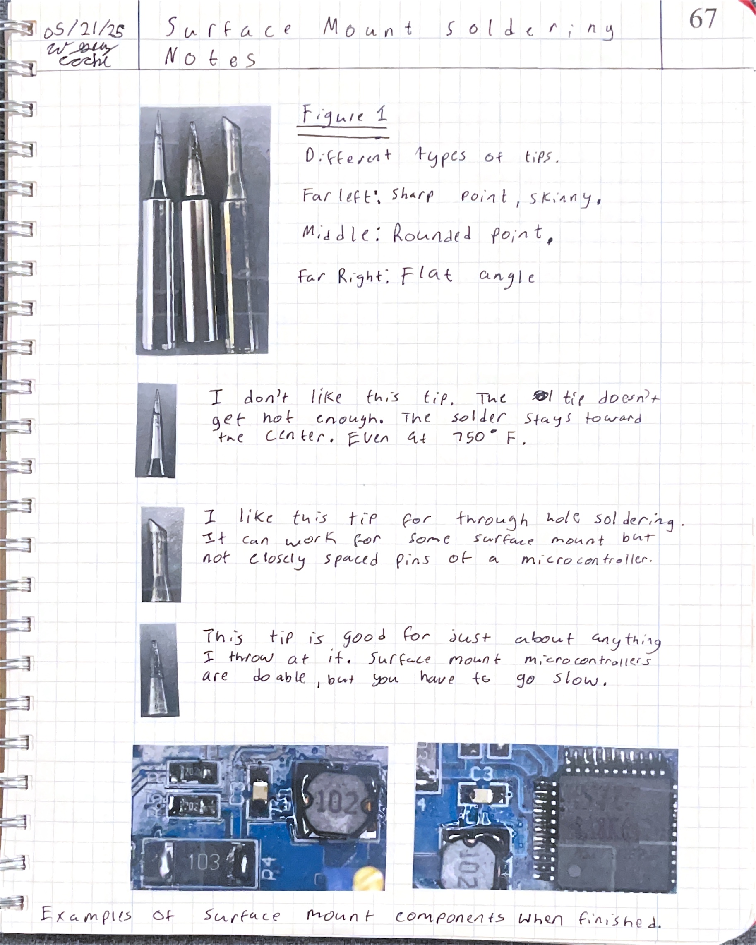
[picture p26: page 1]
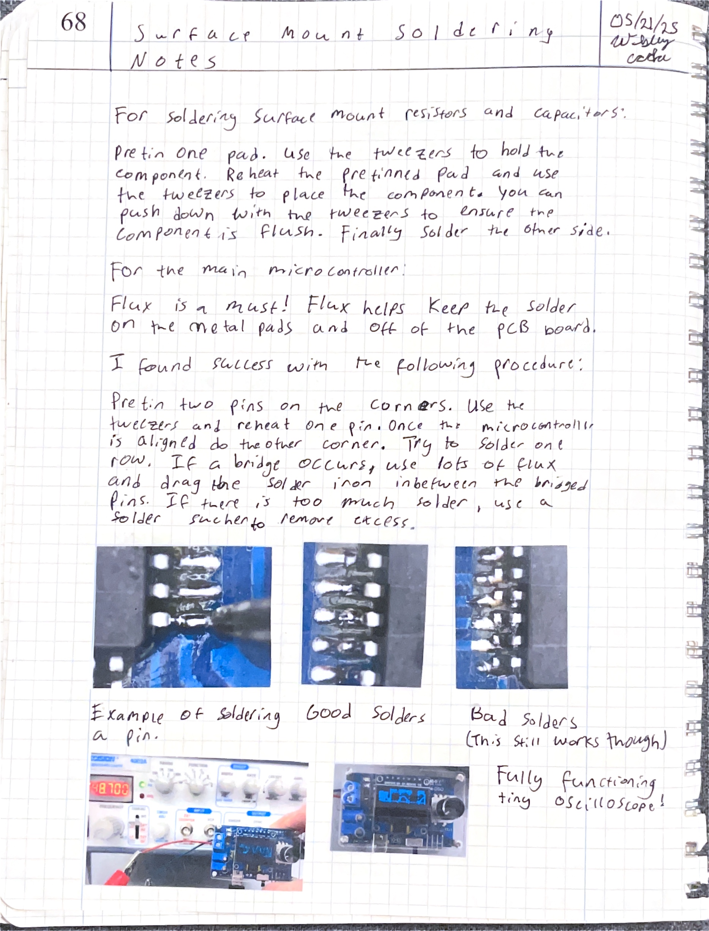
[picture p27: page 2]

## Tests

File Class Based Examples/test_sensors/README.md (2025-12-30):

# Sensors 

We are using four different I²C Atlas scientific sensors and a one-wire DS18B20 temperature sensor.

The Atlas sensors are the Dissolved Oxygen, pH, conductivity, oxidation reduction potential. 

sensors.h contains three main classes 

- `AtlasSensor` - The class we will use for each atlas sensor. The only difference will be the I²C address we use. 
- `TempSensor` - Class that controls the DS18B20 temp sensor
- `WaterMonitor` - A class that coordinates all the Atlas Scientific sensors and the DS18B20 sensor. 

WIL should only have to communicate with the  `WaterMonitor` class. 

To add a new sensor, you should update the `EcoData` struct and the `WaterMonitor` class. As well as adding your own class for the new sensor.

## AtlasSensor Class

The `AtlasSensor` class provides a minimal interface to Atlas Scientific sensors over I²C.

### Key Characteristics
- Uses `Wire2` (separate from the main I²C bus)
- Reads sensor values as ASCII and converts them to `float`

### Typical Usage Pattern
1. Set the sensor address
2. Call `begin()` to verify presence on the I²C bus
3. Call `request()` to trigger a measurement
4. Call `read()` to retrieve the result

## TempSensor Class 

The `TempSensor` class interfaces with a DS18B20 temperature sensor using the OneWire protocol.

### Responsibilities
- Initialize the OneWire bus
- Trigger temperature conversions
- Read and convert raw sensor data to degrees Celsius

### Notes
- The sensor is configured for 10-bit resolution

## Water Monitor Class 

The `WaterMonitor` class is the main abstraction WIL should interact with. It collects data from all sensors and packages it into an `EcoData` struct.

### Responsibilities
- Own and initialize all sensor objects
- Coordinate sensor read timing
- Populate and return a complete `EcoData` struct

### Currently Managed Sensors
- Dissolved Oxygen (DO)
- Oxidation Reduction Potential (ORP)
- pH
- Conductivity
- Water Temperature

## EcoData Struct

The `EcoData` struct (defined in `types.h`) represents a snapshot of all environmental measurements.

Fields include:
- `float conductivity`
- `float DO`
- `float pH`
- `float ORP`
- `float waterTemp`

### Important
If a new sensor is added:
- A new field must be added to `EcoData`
- The `WaterMonitor` class must be updated to populate it

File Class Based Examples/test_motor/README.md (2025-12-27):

# Motor Class for the T200 motors and ESCs

This code provides a simple class for controlling an Electronic Speed Controller (ESC) using a PWM signal. It is written to work with typical RC-style ESCs (such as the BlueRobotics ESC). 

I've named this class Motor even though we are really only talking to the ESC. The ESC handles the motor control. So to our program the ESC is essentially the motor.  

## Big Picture of the Class
- Outputs a PWM signal using the Arduino Servo library 
- Controls motor speed by writing pulse widths in microseconds
- Smoothly ramps motor speed to the target value 
- Clamps commands to proper range 

## ESC Signal 

| Speed (us) | Direction | 
|--- |--- |
|1100-1475 | Reverse |
|1475-1525 | Stopped |
|1525-1900 | Forward |

## Constructor

```cpp
Motor(uint8_t pwmPin, int forward_limit, int reverse_limit, int stop);
```

Parameters:
- pwmPin - Arduino pin connected to the ESC signal. (Look for a ~ on the Arduino). 
- forward_limit - Maximum Forward PWM value in us. (1900 for the Blue Robotics ESC)
- reverse_limit - Maximum reverse PWM value (us) (1100 for Blue Robotics ESC)
- stop - neutral/stop PWM value (1500 for Blue Robotics ESC)

## begin() Method
```cpp
void begin()
```

- Attaches the ESC signal pin using the Servo library. 
- Sends the stop signal 

## updateSpeed() method 
```cpp 
void updateSpeed(int targetSpeed);
```
- Clamps the requested speed to a range that is valid 
- Gradually ramps the current speed to the target speed. This prevents sudden jerks on the motor that sound unpleasant and will damage the motors over time.

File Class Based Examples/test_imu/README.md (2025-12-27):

# BNO055 IMU 

The BNO055 inertial measurement unit uses a combination of an accelerometer, gyroscope, and magnetometer to keep tracking headings from some reference system. 

The `BNO` class does the following: 
- Uses I²C to get data from a BNO055. 
- Configures the BNO to use a IMU fusion mode
    - The gyroscope and accelerometer fusion mode is used for WIL 
    - WIL does not use the magnetometer. In our experiments we found that the magnetometer was too susceptible to noise such as power lines. 
- The BNO class reports a heading in degrees. 
- The heading will be relative to the orientation when the system is powered on. 

When using WIL, it is best to align the system to a desired reference direction before powering on the IMU. 

For small experiments you may wish to align the IMU with the edge of a table. Then you can rotate it by 90 degrees and see if the measurement changed by 90. 

## Class Overview 

### Constructor 
```cpp
BNO(uint8_t address); 
```

Creates a BNO interface using the given address. 

### The begin() method 
```cpp
bool begin(); 
``` 
1. Verifies that a device responds at the given I²C address
2. Sets the BNO055 to IMU mode
    - register: OPR_MODE (0x3D)
3. Configures the angle units to degrees 
    - register: UNIT_SEL (0x3B)

Returns true if initialization succeeds.
Returns false if hte device does not respond. 

### The getHeading() method 
```cpp
float getHeading();
``` 
The heading is read from the Euler X registers. The value is a 16-bit quantity split across two 8-bit registers (LSB and MSB)

- LSB is at 0x1A 
- MSB is at 0x1B 

After combining the bytes, we divide by 16 per the data sheet. If the reading is 16 (0b1000 or 0x10) the heading is 1 degree. So each bit represents 1/16 th of a degree. 

## Notes
There is a calibration that we can check. However, the calibration process is not easy to do on WIL since we can't pick WIL up and move him around easily. We have found that the BNO will 'drift' over time. This drift causes our heading error to accumulate. To solve this we use a heading we get from the GPS to correct the BNO over time. That is not presented here, but is good to know.

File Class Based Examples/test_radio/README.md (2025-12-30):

# Radio Module for remote control features

The radio.h file implements a simple UART radio communication protocol using the Sik Telemetry Radios. 

The Sik radio handles the actual transmission of data over the air, including packetization and error correction. From the perspective of the microcontroller, the radio behaves like a transparent UART link. All we need to do is send and receive bytes over a serial connection.
On top of this, a simple protocol is implemented using header and footer bytes. This helps keep messages synchronized and makes it easier to determine the intent of each packet when it is received.

The 'RadioControl' class is intended to run on the boat side of WIL and is responsible for: 
- Parsing incoming radio packets 
- Storing the most recent received commands or requests 
- Sending responses/data back to the remote control 

## Important design note 
The radio doesn't control the motors directly. Instead it provides received state variables that the rest of the system can act on.
This helps keep communication logic separate from control logic. 

## General Packet Structure 
All packets follow the same high-level format.

`[header][data][footer]`

| Name | Purpose |
|--- | --- |
|header| Single character identifying packet type|
|data  | the actual message data that we care about. This could be a single byte or multiple depending on what is being sent. Generally it will be a specific struct. | 
| footer | Single character identifying the end of the packet. I use the character 'E' |

## Example of Packets the remote sends to the boat 

### Speed Packet
Asks the boat to go a certain speed. 

| | |
|--- |--- |
|Header | 'S' |  
|Data Byte 1  | `int leftMotorRec` |
|Data Byte 2  | `int rightMotorRec`|
|Footer | 'E' |

### Mode Packet 
Informs the boat of what the program mode should be. 

| | |
|--- |--- |
|Header | 'M' |  
|Data Byte 1  | `char modeChar`  |
|Footer | 'E' |

|Mode Values | | 
| --- | --- |
| '0' | AUTONOMOUS | 
| '1' | REMOTE CONTROL| 
| '2' | TUGBOAT | 

The remote dictates the program mode. From the boat’s perspective, the rest of the system checks the `RadioControl` class to determine the current `ProgramMode`.

### Remote Reading Request

Sent from the remote control to the boat.
Signals that the remote control is requesting environmental data. 
Will set a variable called 'takeRemoteReading' to true so the boat knows it needs to take a reading and send it. 'takeRemoteReading' will be set back to false after the data is sent. 

Notice there is no data sent. We just send an 'R' in the header. 
| | |
|--- |--- |
|Header | 'R' |  
|Footer | 'E' |

## Examples of Packets the boat sends to the remote

### EcoData Response
This happens when the flag 'takeRemoteReading' is true. The data is sent as raw bytes using the 

| | |
|--- |--- |
|Header | 'R' |  
|Data Bytes  | EcoData ecoData  (this is one of our structs)|
|Footer | 'E' |

### NavigationState Response 

This is typically sent when in autonomous mode at some rate or at new waypoints. 

| | |
|--- |--- |
|Header | 'C' |  
|Data Bytes  | NavigationState navState (this is one of our structs) |
|Footer | 'E' |

## RadioControl Class Overview

Key public Members: 
- ProgramMode mode: Stores the program state
- int leftMotorRec: the left motor speed we want when in remote control mode. Dictated by the joystick on the controller. 
- int rightMotorRec: the right motor speed we want when in remote control mode. Dictated by the joystick on the controller. 
- bool takeRemoteReading: flag used to force the boat to take a reading of the sensors. Activated by pressing a button on the remote control. 

Key Methods: 
- begin(baud) - initializes the serial radio 
- read() - parse incoming packets 
- sendEcoData() - sends eco data back to the remote control
- sendAutoData - sends a NavigationState struct back to the remote control. 

read() should be called as frequently as possible. Don't write blocking methods or things that risk falling into a loop that can't clear. If this happens, read() will not be able to be called and you may lose control of WIL. 

## Examples

The examples in this folder are intended to be run simultaneously on two different microcontrollers, each connected to a Sik telemetry radio.

- `test_radio_controller` simulates a remote without requiring a physical controller.
- `test_radio_boat` simulates the boat's response to incoming packets.

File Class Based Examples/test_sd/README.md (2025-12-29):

# SD Logging and Path Parsing

This test tests two closely related utilities for WIL: 

1. SDLog Class - a SD car logging interface for GPS, navigation, and water quality data 

2. Path Class - A CSV based waypoint loader for autonomous navigation

These classes handle loading where the boat should go from an SD card path and logging what the boat did. 

## SDLog Class

SDlog is responsible for initializing the SD card and writing the logs. 

| File | Purpose |
| --- | --- |
| GPSData.csv | GPS and Navigation data during autonomous operation |
| ECO.csv | Water quality data during remote control | 
| ECOR.csv | Water quality data during remote control | 

Each file is created if missing and given a header on start. If the file already exists, a new header is appended and new data doesn't overwrite old data. 

### Constructor 
```cpp
SDLog myLog(uint8_t cs)
``` 
You have to provide the Chip Select pin as an input. 

### Changing file names
The file names can be changed to be different. I set them in config.h. 

```cpp
// config.h 
constexpr const char* GPS_DATA_FILE   = "GPSData.csv";
constexpr const char* ECO_DATA_FILE   = "ECO.csv"; 
constexpr const char* ECO_REMOTE_FILE = "ECOR.csv";

// inside main code
myLog.setAutoWaterDataFileName(ECO_DATA_FILE);
myLog.setGPSDataFileName(GPS_DATA_FILE);
myLog.setRemoteWaterDataFileName(ECO_REMOTE_FILE);
``` 

If the SD card isn't creating the file, try making the file name shorter. Don't use spaces and special characters. The SD card is picky with the file names. 

### begin() method 
```cpp
bool success = myLog.begin();
```

- Initializes the SD card
- Creates CSV files if needed
- Writes headers to each file 
- Returns false if SD initialization fails

**SDLog must be initialized before using the Path class.**

### logWaterData() method 
```cpp 
void logWaterData(const Date &date, const Point &location, const EcoData &data, ProgramMode mode) 

myLog.logWaterData(date, position, ecoData, mode);
```
The logWaterData method will select the proper file to log to based on the mode that is passed. 

### logAutonomous() method
```cpp
void logAutonomous(const NavigationState &state, const GlobalPositioningData &data)

myLog.logAutonomous(navState, gpsData);
``` 

Logs the autonomous navigation information including headings, heading errors, gps data, distances to waypoints, etc. Everything member of NavigationState struct and GlobalPositioningData struct are logged. 

## Path Class 

The Path class loads a list of waypoints from a CSV file on the SD card. 

### Expected format
```csv
id,longitude,latitude
1,-830000000,330000000
2,-830000100,330000100
3,-830000200,330000200
```

Coordinates should be in the long format. Not decimal. 
The first line is always treated as a header. The waypoint ID starts at 1. 

### Constructor 
```cpp
Path(int maxLength)
``` 

The maxLength argument sets how big of an array we allocate. I have been configuring this by changing the MAX_WAYPOINTS variable in config.h. 

:TODO: Read the path file to first determine the exact size necessary to allocate for the waypoint arrays. Don't be lazy like me. 

### Parsing the path
```cpp
bool success = myPath.parsePath();
``` 

- Opens 'path.csv' :TODO: Make this not hardcoded
- Loads waypoints into preallocated arrays of length MAX_WAYPOINTS. 
- Returns false if there is some sort of file error. Make sure the file extension is correct and the SD card is inserted. 

### Checking the path over serial monitor 
```cpp
myPath.printPath()
``` 
Prints all loaded waypoints to Serial. Useful for validation before deployment. 

## test_sd.ino
This sketch makes fake GPS, navigation, and sensor data so that you can just test the SD card functionalities without the other sensors connected. Additionally, you can test that each program mode opens the proper file.

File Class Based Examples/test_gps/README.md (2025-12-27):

# GPS Class 

This folder contains a from-scratch GPS driver written in C++ for Arduino. It communicates directly with a u-blox ZED-F9P GPS module over I²C and parses raw binary data into values like latitude, longitude, speed, and heading. 

If you only want GPS data quickly, a library like in the beginner examples is easier to use. 

If you want to understand what the code the Sparkfun library is doing, this is a step in the right direction. The problem is that the official implementation relies on concepts like mutexes. Mutexes are powerful, an excellent tool, and absolutely not something I want to explain in this project.

So this implementation trades completeness and complexity for simplicity. It’s simpler, more readable, but also limited.

## Big Picture of the class

Every call of getData(); will do the following: 

1. Old GPS data is cleared from the I²C buffer. 
2. The GPS is polled for a NAV-PVT message. 
3. The code waits until the GPS has data or a timeout limit is reached. 
4. Assuming there is data, a packet is read from the GPS. 
5. The packet header and checksum are verified
6. Raw bytes are parsed into meaningful values 
7. A `GlobalPositioningData` object is updated 

If any step fails, the data is rejected. 

## File Breakdown 
- `gps.h` 
This files contains the GPS class called `GlobalPositioning`. 

- `test_gps.ino`
This file contains example code of using the class. 

- `types.h`
This file defines the GlobalPositioningData structure. 

- `config.h` 
Contains the I²C address we want to use.

Raw GPS bytes can be printed by enabling 
```constexpr bool DEBUG_PRINT_GPS_DATA = true;```

## The `GlobalPositioning` Class

### Constructor

```cpp
GlobalPositioning(uint8_t address); 
```

Creates a GPS interface using the given address. 

### Public Members 
```cpp
GlobalPositioningData data;
```
Holds the most recently parsed GPS data.

This structure is only updated when a complete, valid packet is received. If packet validation fails, the contents of data remain unchanged. 

---
```cpp
bool begin()
``` 
Checks that a device acknowledges on the I²C bus. 
Does not do any configuration. 

:TODO: extend begin() to configure the GPS too. 

Returns true if the device responds. 
Returns false if no acknowledgement is received.

Be mindful of the snake, young player.
This function does not verify that the responding device is actually the gps. It only verifies that something answered at the given I²C address.

If SneakySnakeSensor happens to share the same address, begin() will still return true. 

`begin()` confirms presence, not identity. 

---
```cpp
int getData();
```
Requests a NAV-PVT message from the GPS and attempts to parse it. 

This method will do the following:
- Clear any stale bytes from the GPS I²C buffer. 
- Polls the GPS until a full packet is available (or a timeout hits) 
- Verifies packet header and payload length
- Computes and checks the UBX checksum 
- Parses raw bytes into the `GlobalPositioningData` structure 

Will return 1 for new valid GPS data
Will return 0 for timeout, checksum fail, or invalid packet.

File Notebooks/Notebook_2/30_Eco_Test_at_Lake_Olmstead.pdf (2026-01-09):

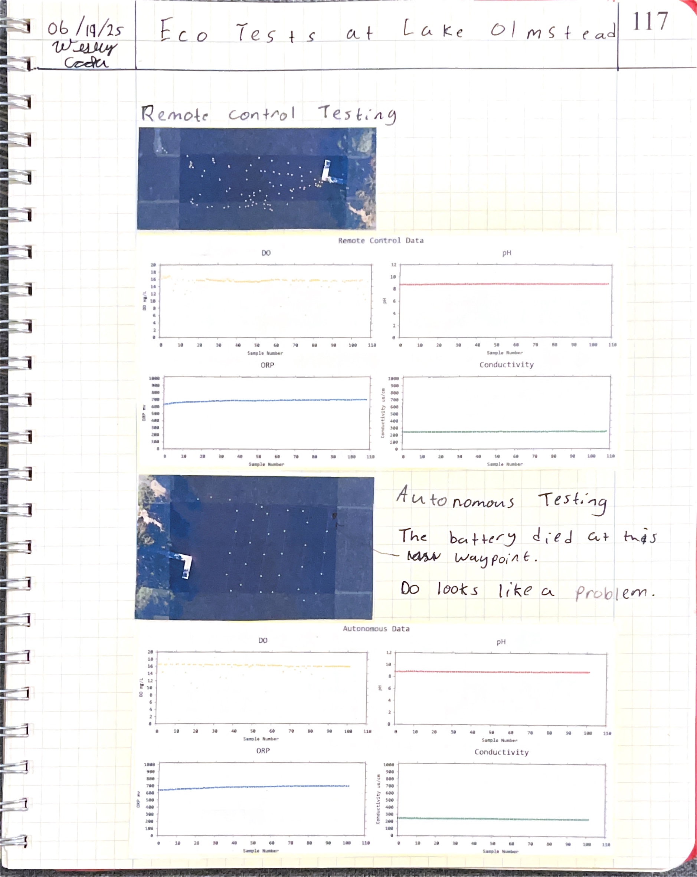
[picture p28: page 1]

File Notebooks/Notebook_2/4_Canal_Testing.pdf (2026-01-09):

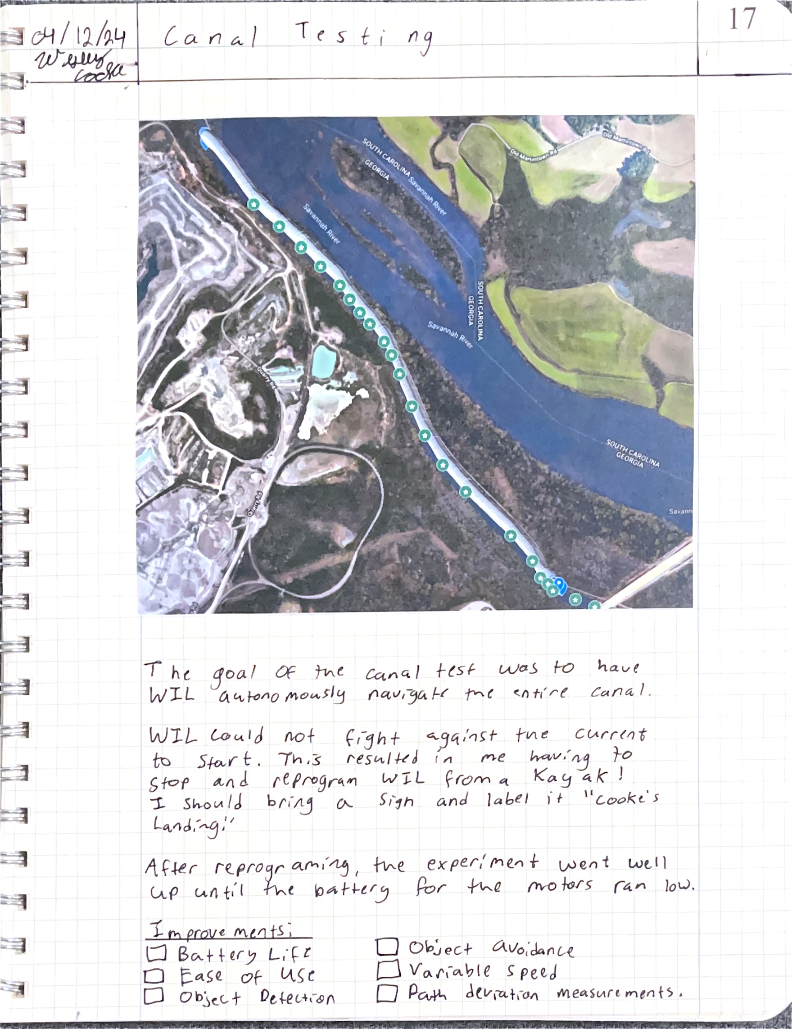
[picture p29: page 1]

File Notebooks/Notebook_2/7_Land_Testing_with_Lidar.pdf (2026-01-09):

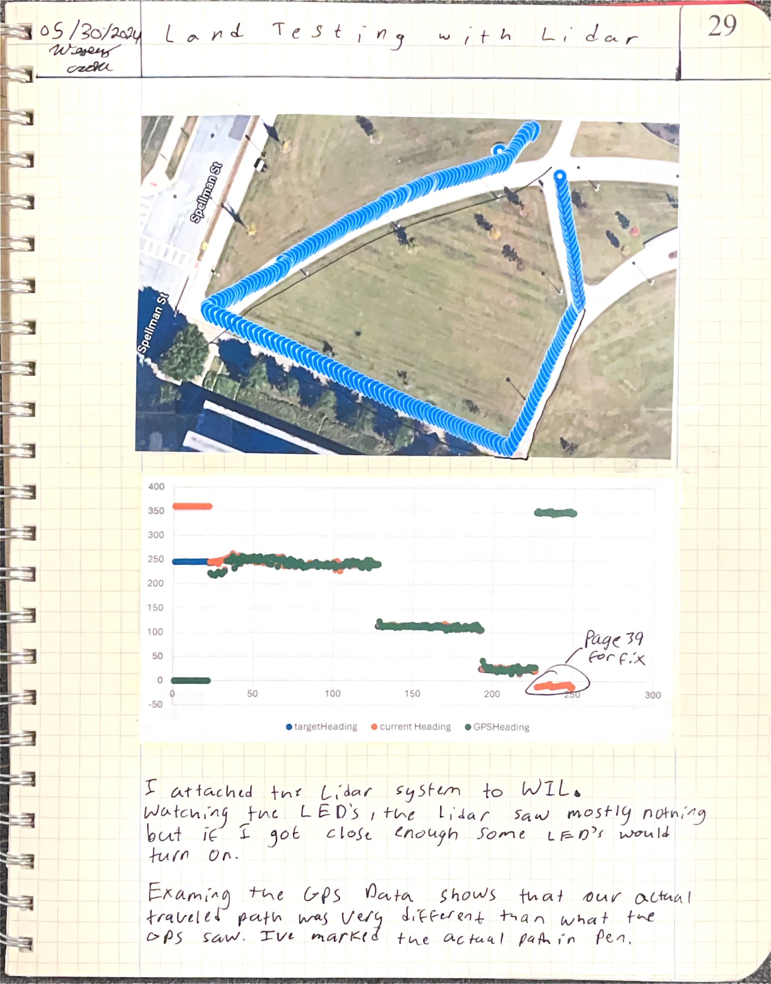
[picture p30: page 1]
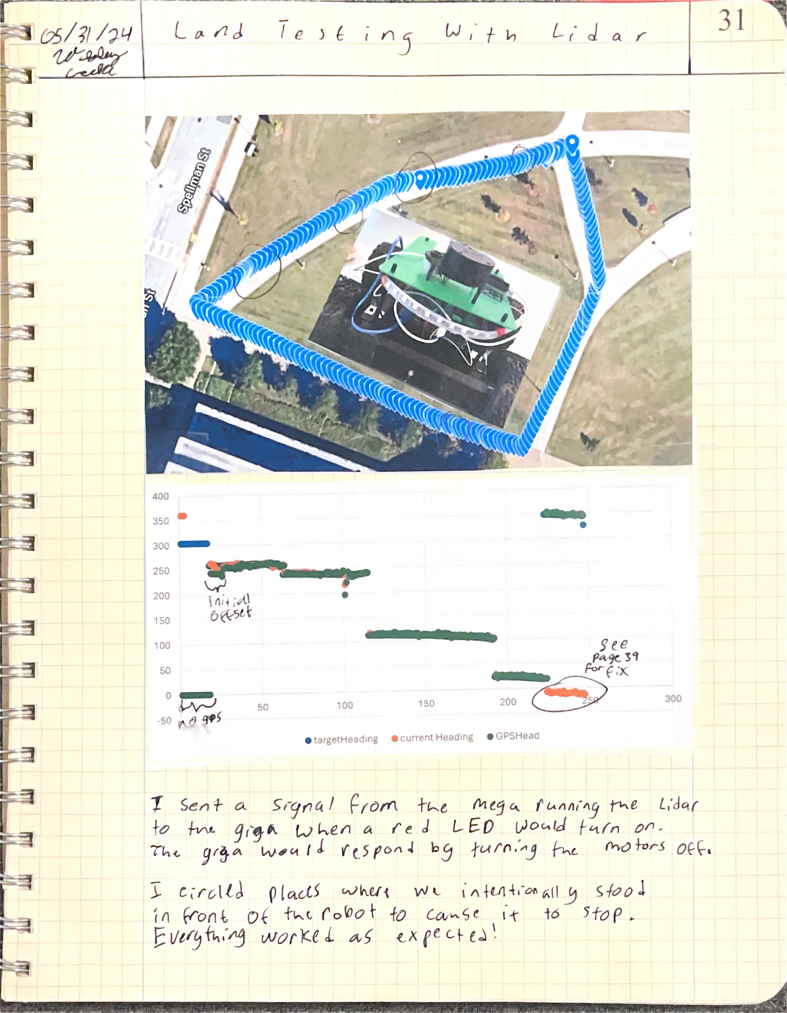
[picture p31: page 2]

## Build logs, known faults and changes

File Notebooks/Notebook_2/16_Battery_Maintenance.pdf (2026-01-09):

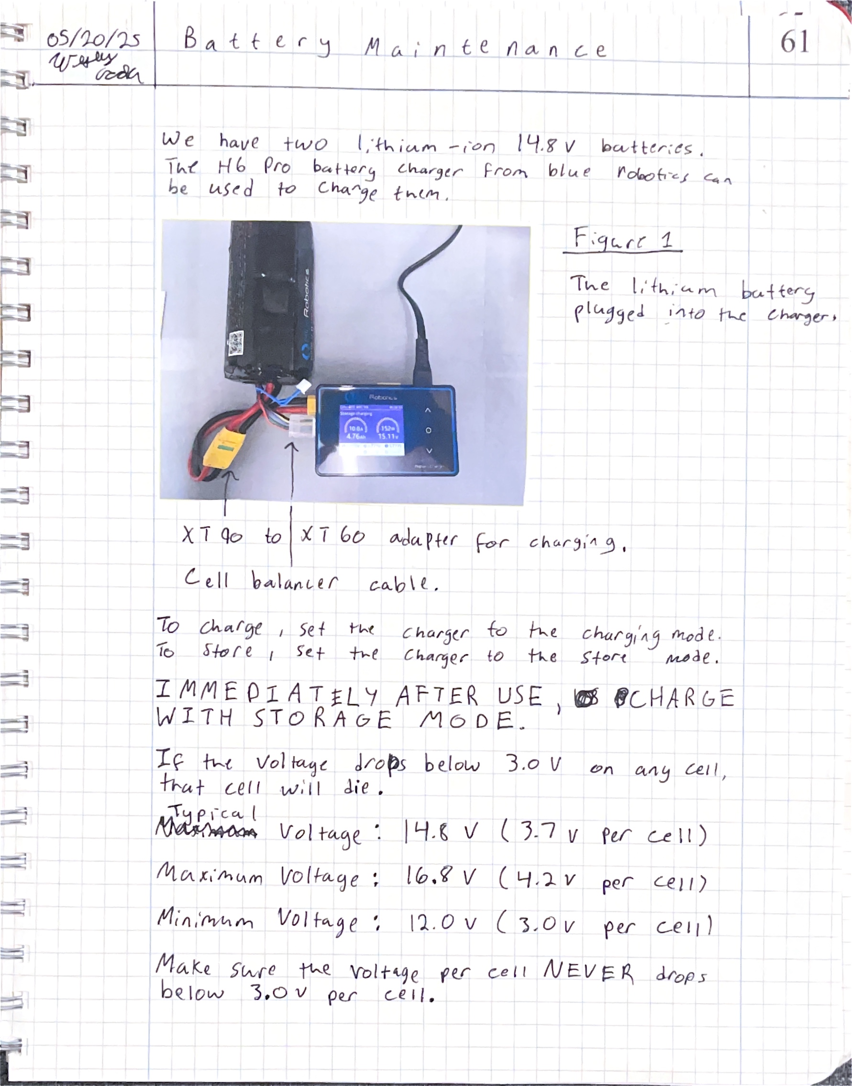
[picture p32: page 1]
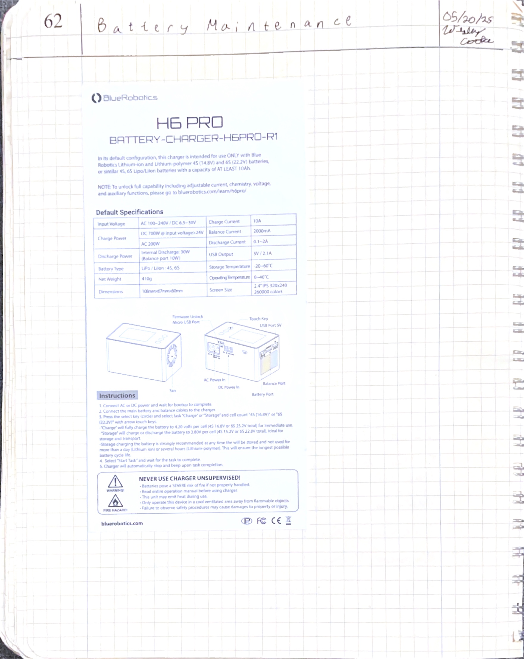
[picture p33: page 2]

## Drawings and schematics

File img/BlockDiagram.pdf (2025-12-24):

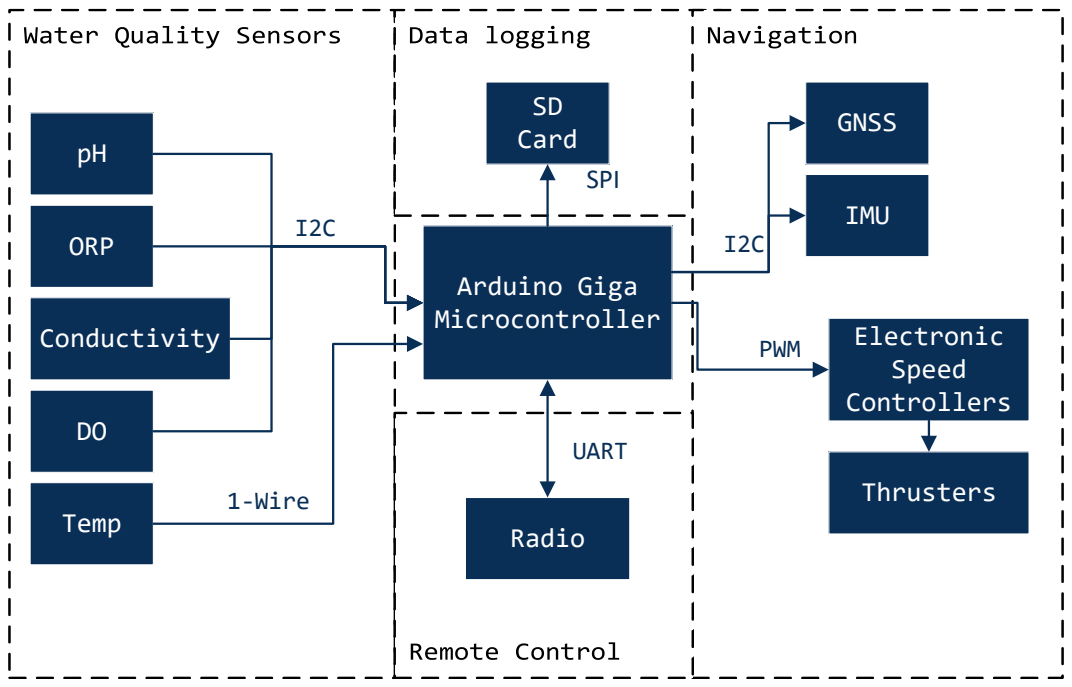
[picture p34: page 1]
Arduino Giga Microcontroller; ORP; Temp; Conductivity; -Wire; Card; GNSS; IMU; Electronic Speed Controllers; Thrusters; Radio; PWM; UART; SPI

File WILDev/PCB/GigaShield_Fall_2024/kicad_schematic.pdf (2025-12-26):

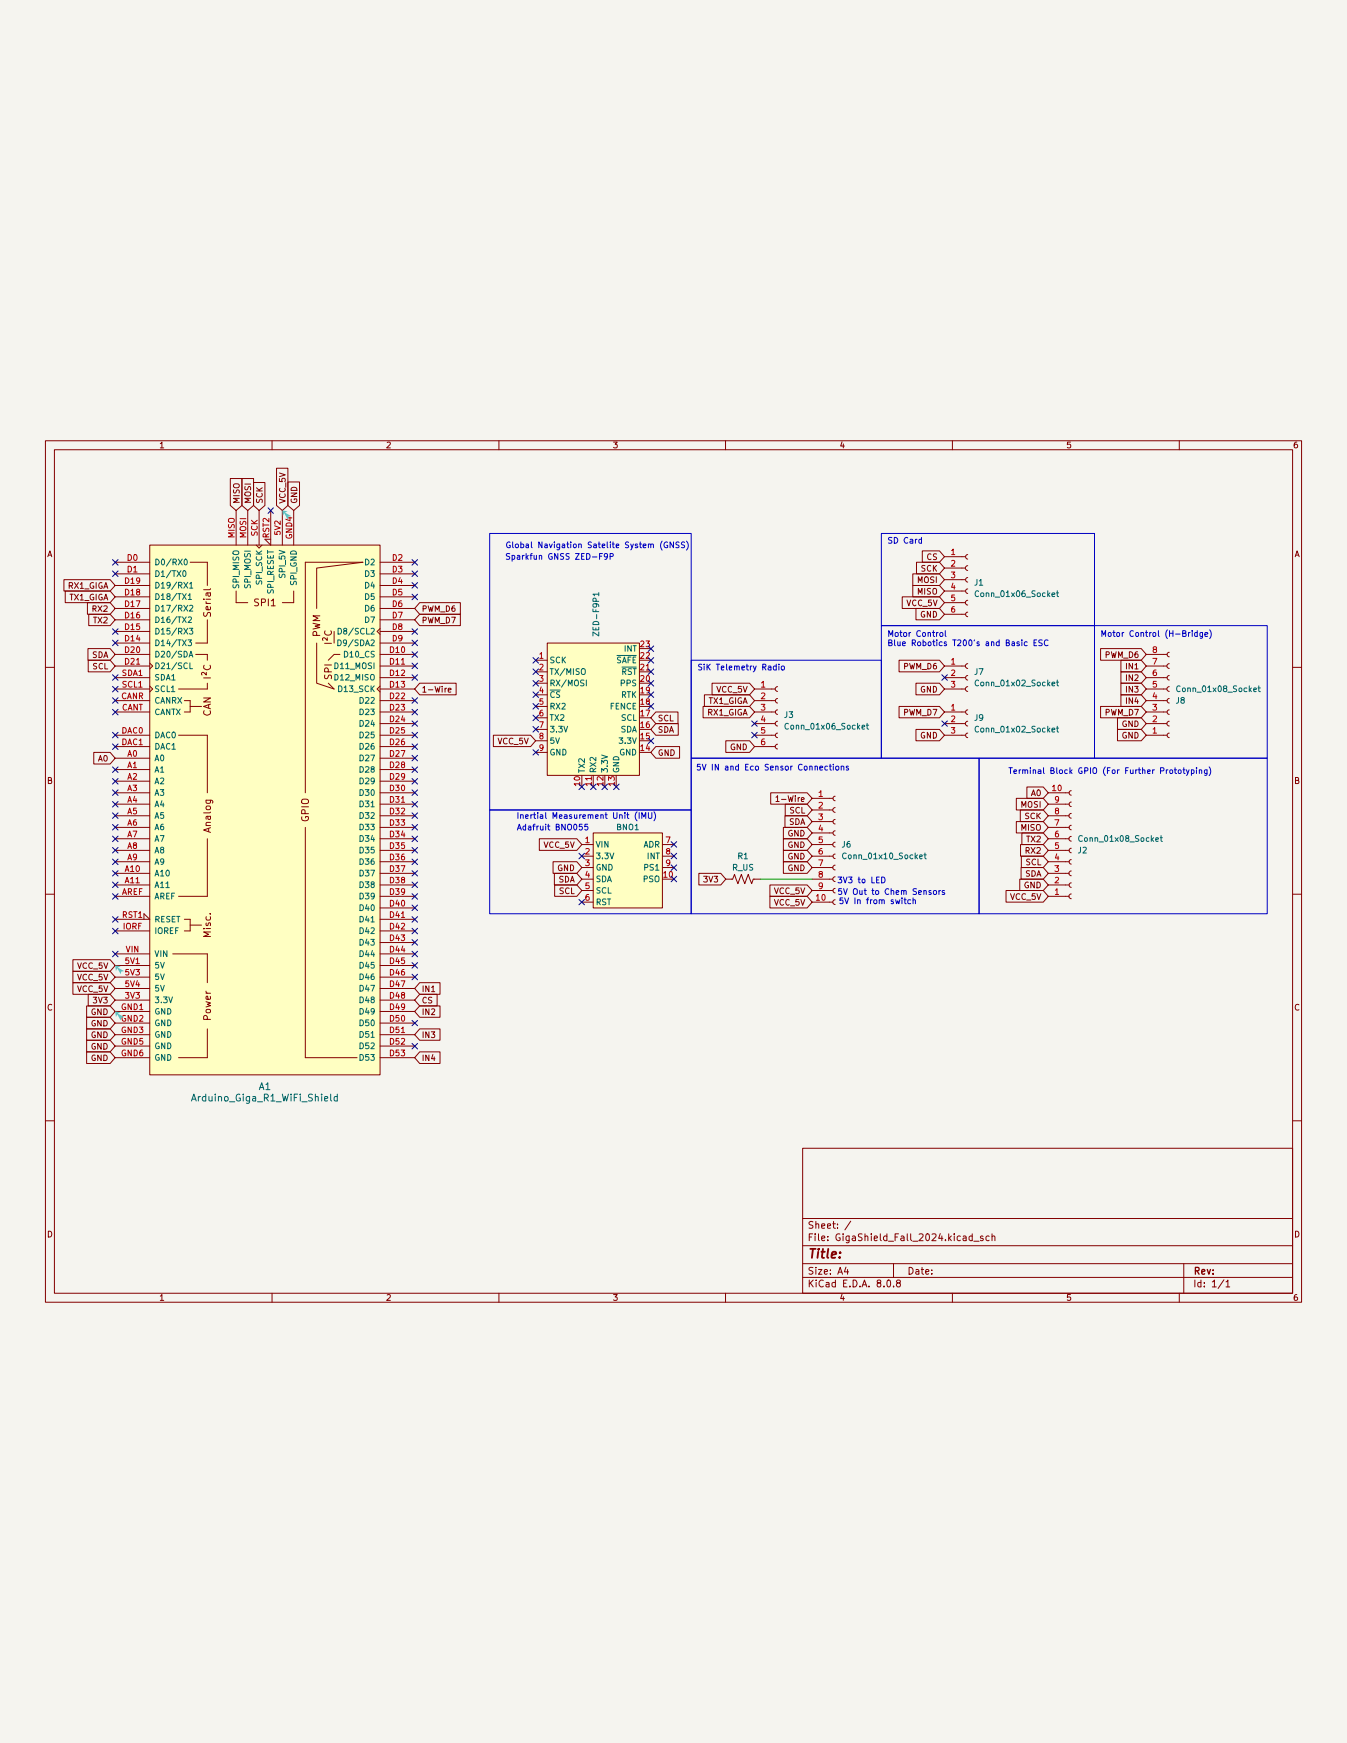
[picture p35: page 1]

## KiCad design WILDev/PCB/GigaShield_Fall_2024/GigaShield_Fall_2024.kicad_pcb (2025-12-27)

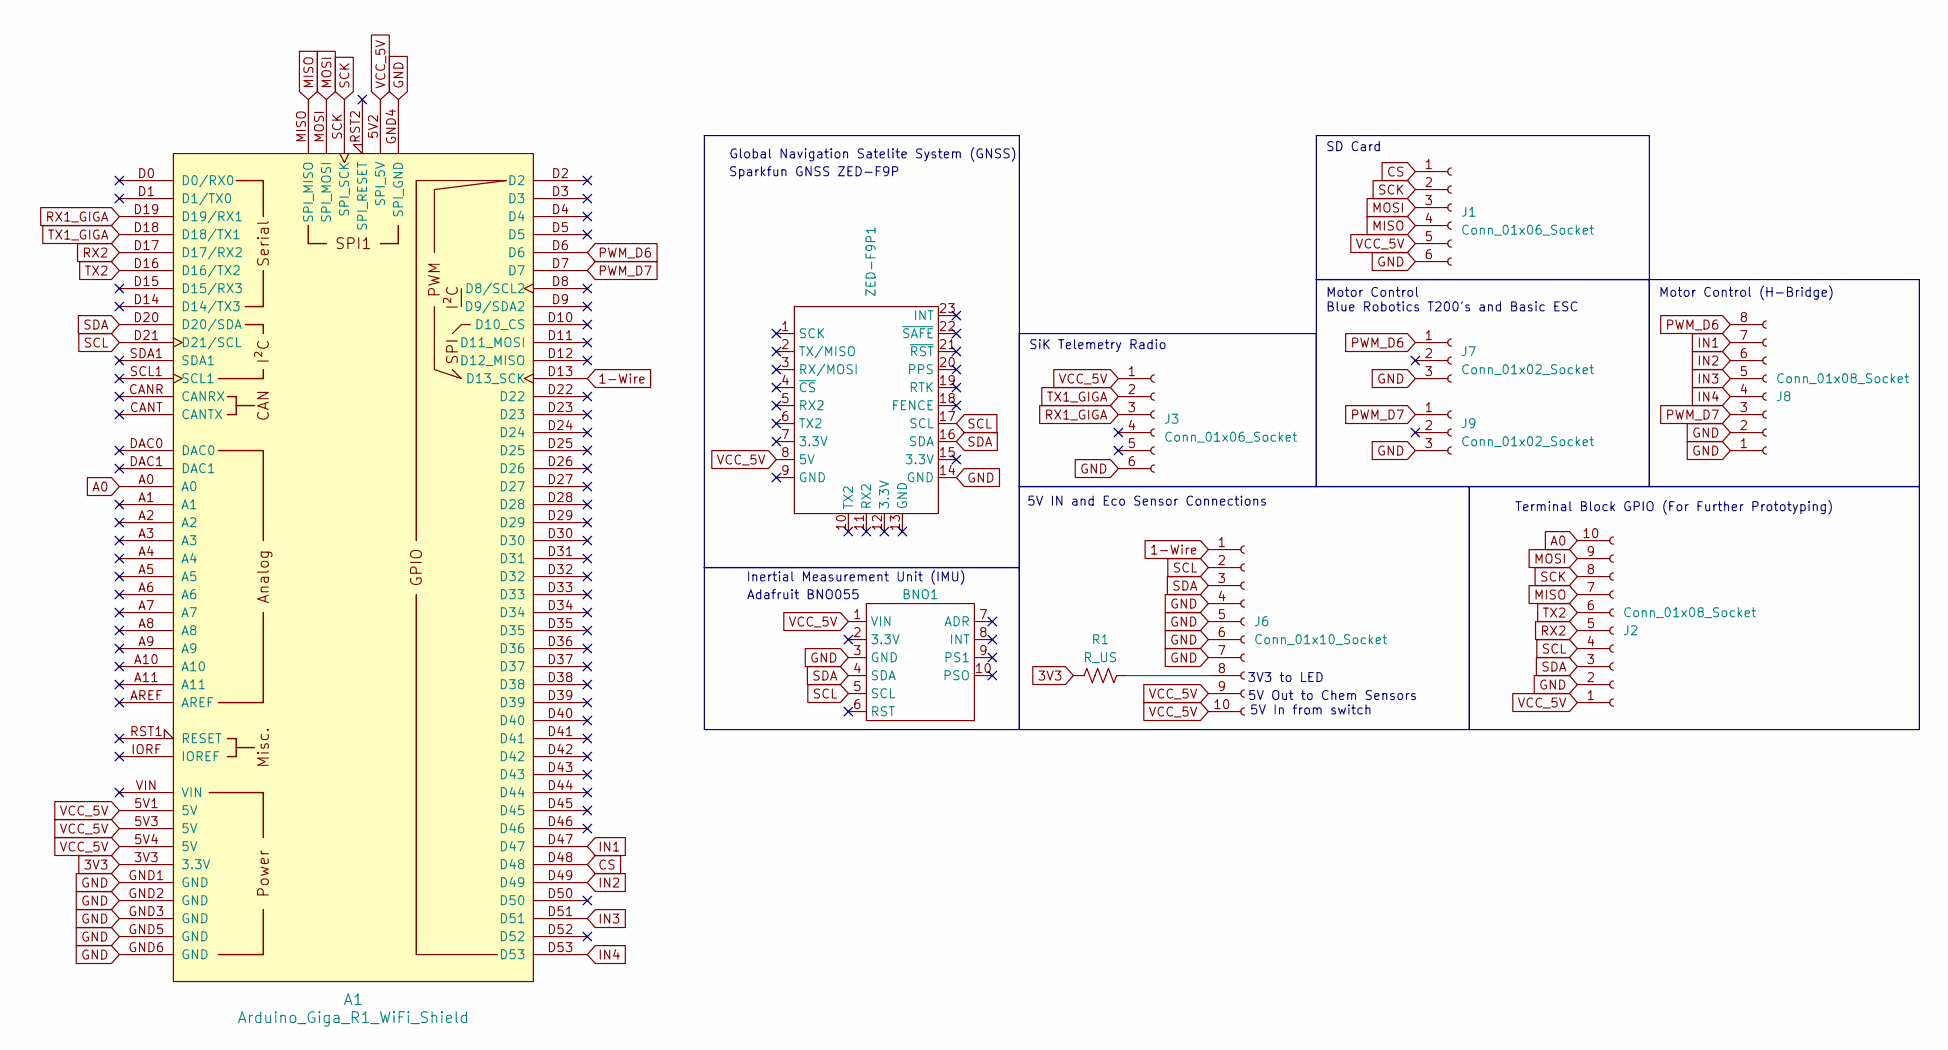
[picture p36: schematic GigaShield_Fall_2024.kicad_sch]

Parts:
A1: Arduino_Giga_R1_WiFi_Shield
BNO1: BNOAdafruit
J1: Conn_01x06_Socket; PinSocket_1x06_P2.54mm_Vertical
J2: Conn_01x08_Socket; TerminalBlock_Xinya_XY308-2.54-10P_1x10_P2.54mm_Horizontal
J3: Conn_01x06_Socket; JST_GH_SM06B-GHS-TB_1x06-1MP_P1.25mm_Horizontal
J6: Conn_01x10_Socket; TerminalBlock_Xinya_XY308-2.54-10P_1x10_P2.54mm_Horizontal
J7, J9: Conn_01x02_Socket; PinHeader_1x03_P2.54mm_Vertical
J8: Conn_01x08_Socket; TerminalBlock_Xinya_XY308-2.54-8P_1x08_P2.54mm_Horizontal
R1: R_US; R_Axial_DIN0309_L9.0mm_D3.2mm_P12.70mm_Horizontal
ZED-F9P1: SparkfunZedF9P

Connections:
1-Wire: A1.D13 (D13_SCK), J6.1
3V3: A1.3V3 (3.3V), R1.1
A0: A1.A0, J2.10
CS: A1.D48, J1.1
GND: A1.GND1 (GND), A1.GND2 (GND), A1.GND3 (GND), A1.GND4 (SPI_GND), A1.GND5 (GND), A1.GND6 (GND), BNO1.3 (GND), J1.6, J2.2, J3.6, J6.4, J6.5, J6.6, J6.7, J7.3, J8.1, J8.2, J9.3, ZED-F9P1.14 (GND)
IN1: A1.D47, J8.7
IN2: A1.D49, J8.6
IN3: A1.D51, J8.5
IN4: A1.D53, J8.4
MISO: A1.MISO (SPI_MISO), J1.4, J2.7
MOSI: A1.MOSI (SPI_MOSI), J1.3, J2.9
unnamed: J6.8, R1.2
PWM_D6: A1.D6, J7.1, J8.8
PWM_D7: A1.D7, J8.3, J9.1
RX1_GIGA: A1.D19 (D19/RX1), J3.3
RX2: A1.D17 (D17/RX2), J2.5
SCK: A1.SCK (SPI_SCK), J1.2, J2.8
SCL: A1.D21 (D21/SCL), BNO1.5 (SCL), J2.4, J6.2, ZED-F9P1.17 (SCL)
SDA: A1.D20 (D20/SDA), BNO1.4 (SDA), J2.3, J6.3, ZED-F9P1.16 (SDA)
TX1_GIGA: A1.D18 (D18/TX1), J3.2
TX2: A1.D16 (D16/TX2), J2.6
VCC_5V: A1.5V1 (5V), A1.5V2 (SPI_5V), A1.5V3 (5V), A1.5V4 (5V), BNO1.1 (VIN), J1.5, J2.1, J3.1, J6.9, J6.10, ZED-F9P1.8 (5V)

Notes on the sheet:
3V3 to LED
Sparkfun GNSS ZED-F9P
Terminal Block GPIO (For Further Prototyping)
5V Out to Chem Sensors
5V In from switch
5V IN and Eco Sensor Connections
Inertial Measurement Unit (IMU)
SiK Telemetry Radio
Motor Control (H-Bridge)
Adafruit BNO055
SD Card
Global Navigation Satelite System (GNSS)
Motor Control Blue Robotics T200's and Basic ESC

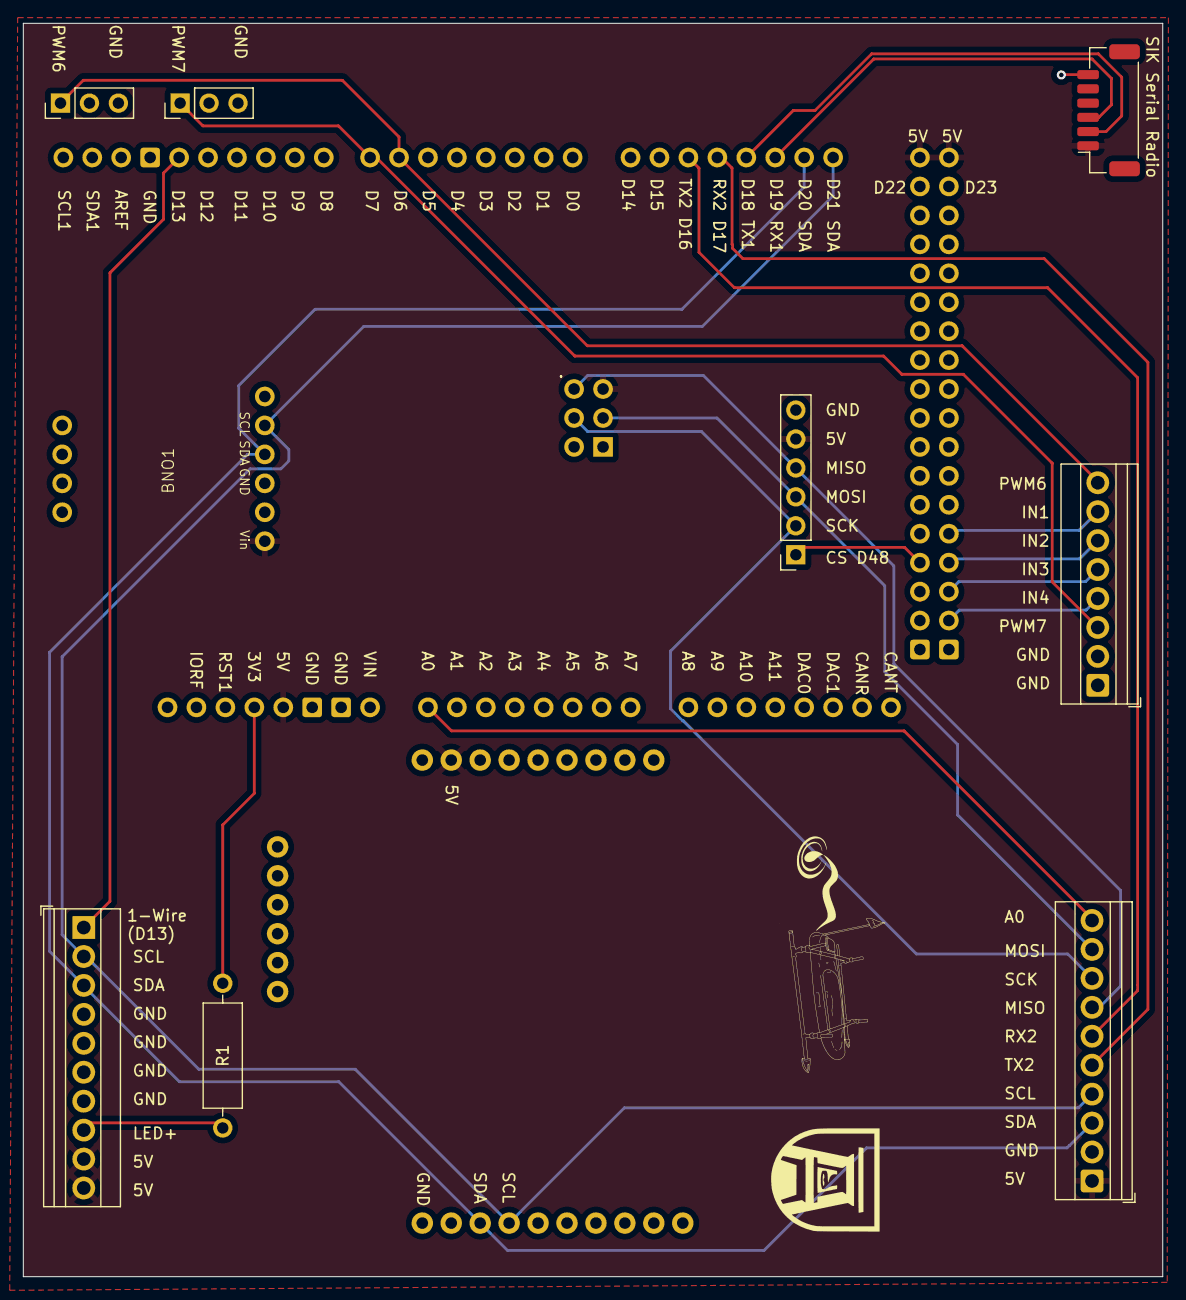
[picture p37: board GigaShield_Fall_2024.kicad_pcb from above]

Board: 2 copper layers, 100.0 x 110.0 mm, 11 parts (0 on the bottom side), 22 nets.

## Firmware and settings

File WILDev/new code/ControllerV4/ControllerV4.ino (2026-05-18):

#include "display.h"
#include "radio.h"

Display display;

const int leftButton  = 1;
const int rightButton = 0;

const int rightJoystick = A0; 
const int leftJoystick  = A1;

const int sdCS = 5;

volatile bool takeRemoteMeasurement;
volatile ProgramMode mode;
Radio remote;

unsigned long speedTimer;
unsigned long modeTimer;
volatile unsigned long extraFunctionTimer; 
volatile unsigned long changeModeTimer; 

int leftSpeed;
int rightSpeed;

int prevLeftSpeed;
int prevRightSpeed;

int SERIAL_RADIO_BAUD = 57600;

void changeProgramMode() // Right button on the controller
{
  if (millis() - changeModeTimer > 500)
  {
    switch(mode)
    {
        case AUTONOMOUS:
            mode = TUGBOAT;
            break;
        case REMOTECONTROL:
            mode = AUTONOMOUS;
            break;
        case TUGBOAT:
            mode = REMOTECONTROL;
            break;
        default:
            break;
    }
    changeModeTimer = millis(); 
  }
}

void extraFunctionButton()
{
    // If we request a eco reading in remote control mode and we haven't requested it for 5 seconds.
  if (takeRemoteMeasurement != 1 && mode == REMOTECONTROL && millis() - extraFunctionTimer > 5000)
  {
    takeRemoteMeasurement = 1;
    extraFunctionTimer = millis();
  }

  if (mode == AUTONOMOUS && millis() - extraFunctionTimer > 2000)
  {
    remote.requestIncrementWaypoint();
    extraFunctionTimer = millis();
  }
}

void setup()
{
    Serial.begin(9600);
    Serial1.begin(SERIAL_RADIO_BAUD);

    analogReadResolution(10);       // 10 bits on analogRead.. max of 1023 
    pinMode(rightJoystick, INPUT);
    pinMode(leftJoystick,  INPUT);
    pinMode(rightButton,   INPUT);
    pinMode(leftButton,    INPUT);

    mode = REMOTECONTROL;
    display.begin();

      // Interrupt for the buttons 
    attachInterrupt(digitalPinToInterrupt(rightButton), changeProgramMode, RISING); 
    attachInterrupt(digitalPinToInterrupt(leftButton), extraFunctionButton, RISING);

    takeRemoteMeasurement = 0;
    speedTimer         = millis();
    modeTimer          = millis();
    extraFunctionTimer = millis();
}

void loop()
{
    remote.read();
    
    // Send the program mode every 1.5 seconds
    if ( (millis() - modeTimer) >= 1500)
    {
        remote.sendMode(mode);
        modeTimer = millis();
    }

    // Send a new speed every 250 miliseconds when in Remote control mode (4 times/second)
    if ( (millis() - speedTimer) >= 250 && mode == REMOTECONTROL)
    {
        readSpeed(); // Updates leftSpeed, rightSpeed; 

        //if (leftSpeed != prevLeftSpeed || rightSpeed!= prevRightSpeed)
            remote.sendSpeed(leftSpeed, rightSpeed);
        
        // prevLeftSpeed  = leftSpeed;
        // prevRightSpeed = rightSpeed
        speedTimer = millis();
    }

    // If we asked for a remote reading
    if (takeRemoteMeasurement)
    {
        remote.requestEcoData();
        takeRemoteMeasurement = 0;
    }

    switch (mode)
    {
      case REMOTECONTROL:
        display.displayRemoteInfo(leftSpeed, rightSpeed, remote.ecoData);
        break;
      case AUTONOMOUS:
        display.displayAutonomous(remote.navState);
        break;
      case TUGBOAT:
        display.displayTugboat();
        break;
      default:
        break;
    }
}

int readSpeed()
{
    // Read the pots
    float forwardBackPercent = analogRead(rightJoystick) / 1023.0;

    // the left joystick is backwards. We can flip it arround
    // by subtracting the raw reading from 1023. 
    // Pushing it to the left causes an increase in the analog read.
    // We need a push to the left to cause a decrease in the analog read. 
    float leftRightPercent   = (1023 - analogRead(leftJoystick)) / 1023.0; 
  
    // Rescale reading. Motor Range is 1100 - 1900. 
    int motorValue = (forwardBackPercent) * 800 + 1100; 
    // Rescale reading. Bias is between -400 and 400. 
    int turnBias   = (leftRightPercent) * 800 - 400;
    
    leftSpeed = motorValue + turnBias; 
    rightSpeed = motorValue - turnBias;

    // Bounds checking... 
    if (leftSpeed > 1900)
      leftSpeed = 1900;
    else if (leftSpeed < 1100)
      leftSpeed = 1100;

    if (rightSpeed > 1900)
      rightSpeed = 1900;
    else if (rightSpeed < 1100)
      rightSpeed = 1100; 
}

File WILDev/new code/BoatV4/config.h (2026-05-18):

#ifndef CONFIG_H
#define CONFIG_H 
    /* ===================================================================================
        These variables are ones that may be useful to change at some point in time.
        I've grouped them together in this file. As a design principle, I didn't want these hard 
        coded into the classes. Instead, the class should own it's own copy. This makes the 
        classes reusable in other code independint of this config file. 

        The keyword "const" is useful to ensure a value is not changed at run time. 
        The keyword "constexpr" is useful to ensure a value is not changed at compile time.
       ====================================================================================*/

    /* =============
        Debug Flags
       ============= */
    constexpr bool DEBUG_PRINT_GPS_DATA = false;
    constexpr bool DEBUG_PRINT_SD_LOG   = true;
    constexpr bool DEBUG_PRINT_SERIAL   = false;

    /* ================
        Path Constants
       ================ */
    constexpr int MAX_WAYPOINTS = 200;
    constexpr int WAYPOINT_DISTANCE_THRESHOLD = 6.0; // 6 meters 

    /* ===========================
        Heading Control Constants
       =========================== */
    constexpr double ACCEPTABLE_HEADING_ERROR = 0.02;
    constexpr int HEADING_AVERAGE_LIMIT    = 100;
    
    /* =================
        Serial Settings
       ================= */
    constexpr unsigned long SERIAL_RADIO_BAUD = 57600;
    constexpr unsigned long DEBUG_SERIAL_BAUD = 9600;

    /* ===============
        I2C Addresses
       =============== */
    constexpr uint8_t   GPS_I2C_ADD = 0x42; 
    constexpr uint8_t  ATLAS_DO_ADD = 0x61;
    constexpr uint8_t ATLAS_ORP_ADD = 0x62;
    constexpr uint8_t  ATLAS_PH_ADD = 0x63;
    constexpr uint8_t   ATLAS_C_ADD = 0x64;
    constexpr uint8_t       BNO_ADD = 0x28;

    constexpr int I2C_TIMEOUT_MS = 100;

    /* =====================
        Sensor Configs 
       =====================*/
    constexpr int ATLAS_SENSOR_DELAY_MS = 1000; // How long each atlas sensor has to wait before getting data.
    constexpr int ONE_WIRE_BUS = 13;

    /* =========
        SD Card 
       ========= */
    constexpr int SD_CHIP_SELECT = 48;
    constexpr const char* GPS_DATA_FILE   = "GPSData.csv";
    constexpr const char* ECO_DATA_FILE   = "ECO.csv"; 
    constexpr const char* ECO_REMOTE_FILE = "ECOR.csv";
    constexpr const char* PATH_FILE       = "path.csv";

    /* =======================
        ESC Control Variables
       ======================= */
    constexpr int LEFT_MOTOR_PIN  = 6;         // Must be a PWM 
    constexpr int RIGHT_MOTOR_PIN = 7;         // Must be a PWM
    constexpr int MOTOR_SETUP_DELAY_MS = 5000; // Delay to allow ESC startup 
    constexpr int ESC_STOP_SIGNAL  = 1500;     // Neutral Speed 
    constexpr int ESC_FULL_FORWARD = 1900;     // Full Throttle Forward
    constexpr int ESC_FULL_REVERSE = 1100;     // Full throttle reverse
    constexpr int ESC_UPDATE_DELAY_US = 20;    // Delay between ESC updates to make smooth changes 

    constexpr int ESC_ROTATE_FORWARD  = 1700;
    constexpr int ESC_ROTATE_REVERSE  = 1280;
    constexpr int ESC_FORWARD         = 1650;
    constexpr int ESC_INIT_TIME_MS    = 3000;

    /* =========================
        RGB LED Pin Assignments
       ========================= */
    constexpr int RGB_R = 86;
    constexpr int RGB_G = 87;
    constexpr int RGB_B = 88;

    /* =========================
    Remote Control Constants
    ========================= */
    constexpr unsigned long MAX_WAIT_MS = 500; // Ammount of time to wait for full packet to be recieved before moving on. 
    constexpr unsigned long CONTROLLER_POLLING_MS = 100; // How often to poll the controller 

    constexpr unsigned long GPS_POLLING_MS = 800;
    constexpr unsigned long GPS_ERROR_POLLING_MS = 8000; // Wait 8 seconds before updating our heading error
#endif

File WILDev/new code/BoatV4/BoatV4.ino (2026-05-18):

#include "boat.h"
#include "utility.h"

Boat boat;

unsigned long pollControllerTimer;  

void setup()
{
    setupI2C();
    
    if (DEBUG_PRINT_SERIAL)
    {
      Serial.begin(DEBUG_SERIAL_BAUD); 
      Serial.println("Begain Serial Print for debugging.");
      Serial.println("==================================");
      Serial.println("I2C Scan:");
      i2cDetect();
      Serial.println("=================================="); 
    }
     
    boat.begin();

    pollControllerTimer = millis();
}

void loop()
{
    if( (millis() - pollControllerTimer) > CONTROLLER_POLLING_MS)
    {
        boat.remote.read();
        pollControllerTimer = millis();
    }

    switch (boat.remote.mode)
    {
        case REMOTECONTROL:
            boat.handleRemote();
            break;
        case AUTONOMOUS:
            boat.handleAuto(); 
            break;
        case TUGBOAT:
            boat.handleTugboat();
            break;
        default: 
            break;
    }
}

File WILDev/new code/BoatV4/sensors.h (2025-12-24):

#ifndef ATLAS_H
#define ATLAS_H

    // This file defines the classes that work with the sensors we are using to monitor the water. 

    #include "types.h"
    #include <Wire.h>
    #include <OneWire.h>
    #include <DallasTemperature.h>

    class AtlasSensor
    {
        public: 
            AtlasSensor()
            {
                // Not passing in the address to start because of the WaterMonitor class. 
                // Forcing us to use the setAddress method
                address = 0;
            }

            void setAddress(uint8_t add)
            {
                address = add;
            }

            bool begin()
            {
                Wire2.beginTransmission(address); 
                uint8_t reply = Wire2.endTransmission();
                
                // The I2C bus sits high. If a device pulls it low, reply will be 0. This indicates a device is at this address.
                // If reply is 0 it indicates success, so we return !0 = 1. !1 = 0, for fail.
                return !reply; 
            }

            void request()
            {
                Wire2.beginTransmission(address);
                Wire2.write('R');         // (R)ead
                Wire2.endTransmission();
            }

            float read()
            {
                Wire2.requestFrom(address, 20);
                uint8_t code = Wire2.read();
                char sensorData[19];
                
                // Code values
                // 1 is success
                // 2 syntax error
                // 254 not ready
                // 255 no data to send
                
                if (code == 1)
                {   
                    // Read the data from the sensor
                    for (int ii = 0; ii < 19; ii++)
                    {
                        char charIn = Wire2.read();
                        sensorData[ii] = charIn;
                    }
                    // Parse the data
                    float sdata = atof(sensorData);

                    return sdata;
                }
                for (int ii =0; ii<19; ii++)
                {
                    Wire2.read(); // Clear out our junk that we requested. 
                }
                return code;
            }
        private: 
            uint8_t address; 
    };

    class TempSensor
    {
        // Class for the DS18B20 
        public: 
            TempSensor()
            {}
            
            void begin(uint8_t pin)
            {
                ds.begin(pin); 
                ds.search(addr);
                ds.reset();
            }

            float get()
            {
                ds.select(addr); // Select our device using its address
                ds.write(0x4E);  // Wirte our configuration to the scratch pad
                ds.write(0x00);  // This is the TH alarm, not using
                ds.write(0x00);  // This is the TL alarm, not using
                ds.write(0x3F);  // Sets to 10 bit resoltuion; see page 9 of the datasheet
                ds.write(0x48);  // Copies the contents of the scratch pad 
                ds.reset(); 
                
                // Measure and read
                ds.select(addr); // Select our device (again!)
                ds.write(0x44);  // This initiates a temperature conversion! 
                delay(200);      // Let it finish conversion (187.5 ms)
                ds.reset();      
                ds.select(addr); // Select it (yes again!)
                ds.write(0xBE);  // Read the scratch pad

                for(int ii=0; ii<9; ii++)
                {
                    data[ii] = ds.read(); // Read the bytes
                }

                uint16_t raw = (data[1]<<8) | data[0]; 
                // Clear bits 1 and 0 since we are using 10-bit resolution
                raw &= ~0x03;
                // Convert to temperature in Celsius 
                float celsius = raw/16.0;

                return celsius;
            }
        private: 
            OneWire ds;
            byte addr[8];
            byte data[9]; 
    }; 

    class WaterMonitor
    {
        public: 
            AtlasSensor DO;
            AtlasSensor ORP;
            AtlasSensor pH;
            AtlasSensor conductivity;
            TempSensor temp;
            
            WaterMonitor(uint8_t DO_add, uint8_t ORP_add, uint8_t pH_add, uint8_t c_add, uint8_t wire_bus)
            {
                DO.setAddress(DO_add);
                ORP.setAddress(ORP_add);
                pH.setAddress(pH_add); 
                conductivity.setAddress(c_add);
                temp.begin(wire_bus);
            }

            // Since we manually allocated memory, we must deallocated it in the destructor. 
            ~WaterMonitor()
            {
                delete &DO;
                delete &ORP;
                delete &pH;
                delete &conductivity;
                delete &temp;
            }

            bool begin()
            {
                bool do_ret = DO.begin();
                bool orp_ret = ORP.begin();
                bool pH_ret = pH.begin();
                bool conductivity_ret = conductivity.begin(); 

                uint8_t reply = do_ret && orp_ret && pH_ret && conductivity_ret;  // If any are false, we failed. 

                return reply;
            }

            const EcoData& getData()
            {
                DO.request();
                ORP.request();
                pH.request();
                conductivity.request();

                delay(ATLAS_SENSOR_DELAY_MS); // Give sensors time to respond
                
                data.waterTemp = temp.get();
                data.DO  = DO.read();
                data.ORP = ORP.read();
                data.pH  = pH.read();
                data.conductivity = conductivity.read();

                return data;
            }

            private:
                EcoData data;
    }; 

#endif

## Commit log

2025-02-02 Adding SD Card Examples
    [path.csv]
2025-12-24 Updating Repo Code
    [path.csv]
2025-12-26 Updating readme
    [ButtonExtension.step, ButtonExtension.x_t, CompassMount.step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]
2025-12-27 Updating PCB Files
    [GigaShield_Fall_2024.kicad_pcb]
2025-12-27 Updated IMU readme
2025-12-27 Updating motor readme
2025-12-30 Updating Sensors Readme
2026-01-11 updating BegEx.
    [path.csv]
2026-05-18 Fixing bug in blinky debuging
    [BoatV4.ino, ControllerV4.ino, boat.h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]
2026-05-18 Adding URFA Data
    [Circle1.xlsx, Circle2.xlsx, Elipse1.xlsx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]
